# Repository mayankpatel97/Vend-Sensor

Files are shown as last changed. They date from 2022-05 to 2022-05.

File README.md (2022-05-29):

Vend sensor is used to detect an item has vend in Vending Machines. It sense the product and send a signal to 
the main motherboard, indicating item has vend. Responding to this signal motherboard will stop rotating motor

Every vending machine has a rectangular bucket from where user collects the purchased items. This sensor will 
be installed there, so it can detect and count each and every product dropped by machine in to the bucket.

A vend sensor must be sensitive and fast enough to detect even tiny products. 

The product has two pcbs 
1) Transmitter : An array IR LEDs transmitting a 56Khz modulated signal. This pcb is connected with Receiver board through a cable
2) Receiver : This board consist of IR demodulators connected to an STM32F0 microcontroller.

************************** PCB ****************************************
Receiver PCB 




Transmitter PCB 



************************* Software *************************************

As I mentioned above the circuit is built around STM32F0 microcontroller, it uses HAL drivers.
Follow below steps to make the code working 

1) Download the code and open STM32 Cube file and regenerate the code.
2) Once the code has generated, open the project in keil MDK ARM, and build the code.
3) Then upload the code in the microcontroller. 

for further details contact me at 
mayankpatel468@gmail.com 
or send a whatsapp message on 
+918802846486

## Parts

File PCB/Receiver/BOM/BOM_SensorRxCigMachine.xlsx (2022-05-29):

S.No | Designator | Value | Description | QTY
1 | > C1-C8, C19-C24 | 0.1uF | Capacitor_SMD:C_0805_2012Metric_Pad1.15x1.40mm_HandSolder | 14
2 | > C9, C10 | 10uF | Capacitor_SMD:C_0805_2012Metric_Pad1.15x1.40mm_HandSolder | 2
3 | > C16, C27 | 100uF/25V | Capacitor_THT:CP_Radial_D6.3mm_P2.50mm | 2
4 | D1 | M7 | Diode_SMD:D_SMA | 1
5 | D3 | GREEN | LED_SMD:LED_0805_2012Metric_Pad1.15x1.40mm_HandSolder | 1
6 | D4 | YELLOW | LED_SMD:LED_0805_2012Metric_Pad1.15x1.40mm_HandSolder | 1
7 | > H1, H2 | MountingHole | MountingHole:MountingHole_3.2mm_M3_Pad | 2
8 | J1 | Conn_01x03 | Connector_Molex:Molex_KK-254_AE-6410-03A_1x03_P2.54mm_Vertical | 1
9 | J2 | Conn_02x05_Odd_Even | Connector_PinHeader_1.27mm:PinHeader_2x05_P1.27mm_Vertical | 1
10 | J3 | Conn_01x05 | Connector_PinHeader_2.54mm:PinHeader_1x05_P2.54mm_Vertical | 1
11 | Q2 | BC847 | Package_TO_SOT_SMD:SOT-23 | 1
12 | > R3, R9 | 330E | Resistor_SMD:R_0805_2012Metric_Pad1.15x1.40mm_HandSolder | 2
13 | > R5, R7, R11, R12, R15-R18 | 100E | Resistor_SMD:R_0805_2012Metric_Pad1.15x1.40mm_HandSolder | 8
14 | R8 | 1K | Resistor_SMD:R_0805_2012Metric_Pad1.15x1.40mm_HandSolder | 1
15 | R10 | 10K | Resistor_SMD:R_0805_2012Metric_Pad1.15x1.40mm_HandSolder | 1
16 | > U1-U8 | TSSP4056 | Apogee:tssp4056 | 8
17 | U14 | LD1117S33TR_SOT223 | Package_TO_SOT_SMD:SOT-223-3_TabPin2 | 1
18 | U15 | STM32F030C8Tx | Package_QFP:LQFP-48_7x7mm_P0.5mm | 1

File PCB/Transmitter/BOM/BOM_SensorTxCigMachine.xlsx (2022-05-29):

S.No | Designator | Value | Description | QTY
1 | D1-D8 | IR204A | LED_THT:LED_D5.0mm_IRBlack | 8
2 | H1, H2 | MountingHole | MountingHole:MountingHole_3.2mm_M3_Pad | 2
3 | J1 | Conn_02x05_Odd_Even | Connector_PinSocket_1.27mm:PinSocket_2x05_P1.27mm_Vertical | 1
4 | R1 | R_US | LED_SMD:LED_0805_2012Metric_Pad1.15x1.40mm_HandSolder | 1

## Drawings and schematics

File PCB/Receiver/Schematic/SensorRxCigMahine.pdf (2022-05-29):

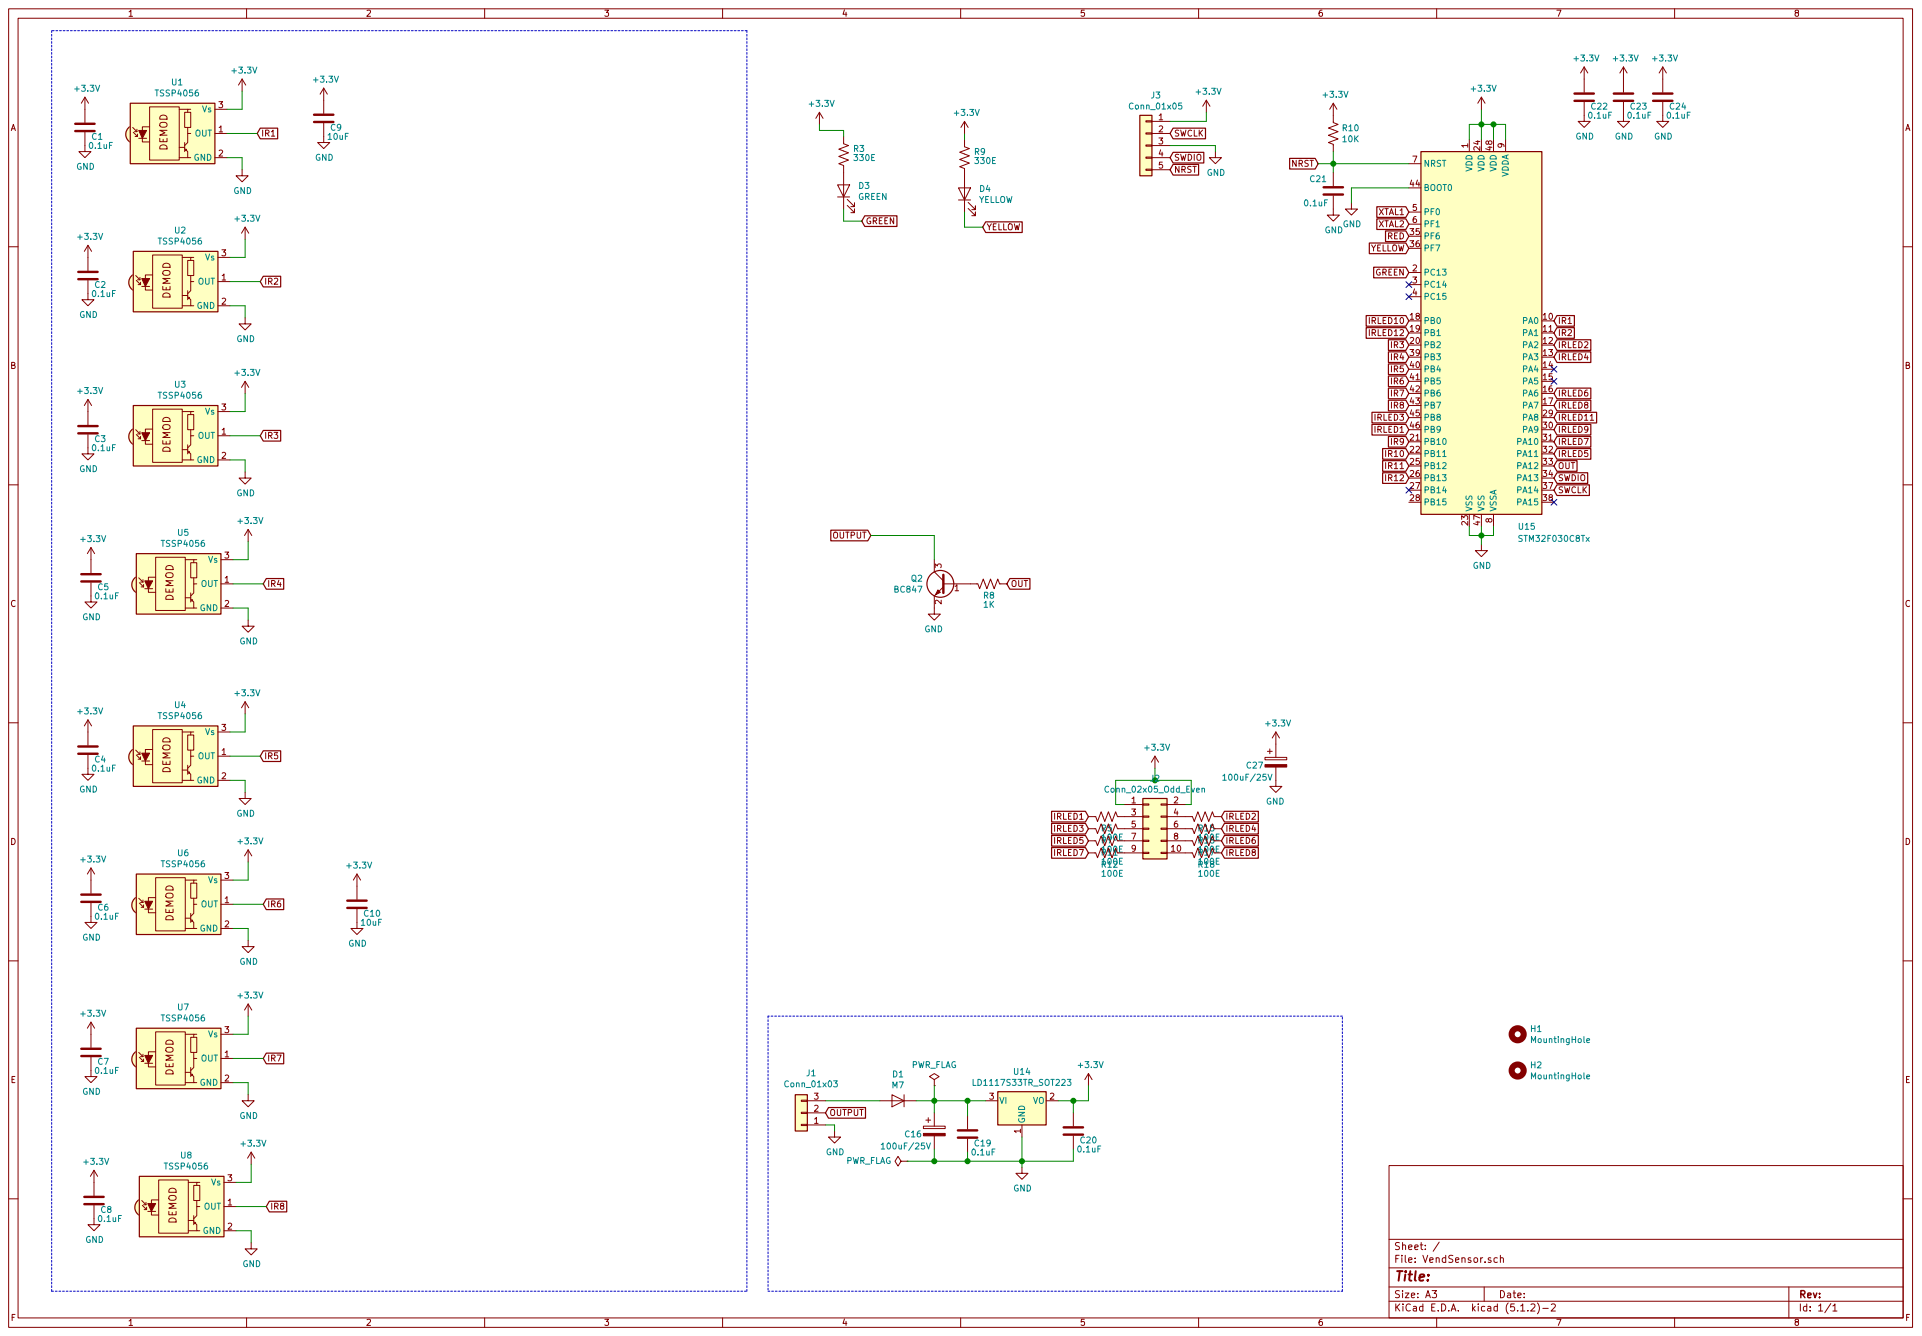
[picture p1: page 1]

PWR_FLAG
Id: 1/1 Title: File: VendSensor.sch Sheet: / D1 M7 C16

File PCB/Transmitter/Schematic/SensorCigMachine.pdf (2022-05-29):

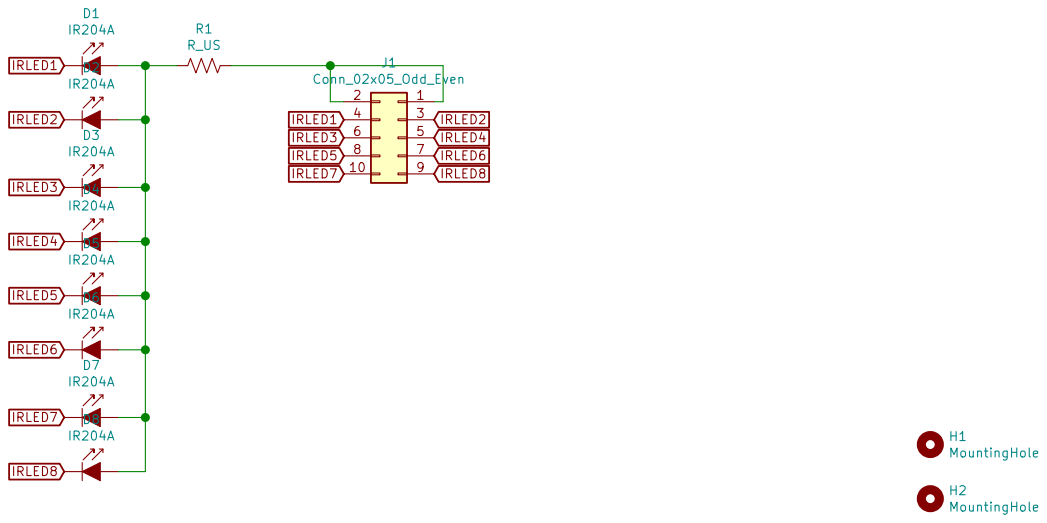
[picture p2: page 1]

Id: 1/1 Title: File: VendSensor.sch Sheet: /

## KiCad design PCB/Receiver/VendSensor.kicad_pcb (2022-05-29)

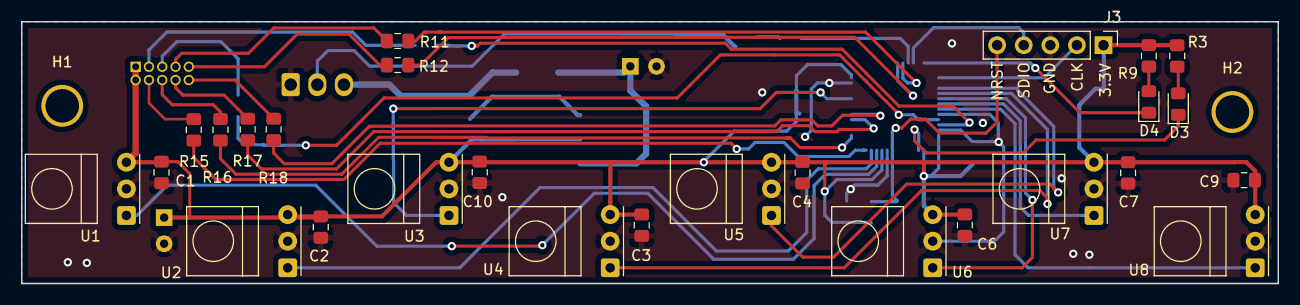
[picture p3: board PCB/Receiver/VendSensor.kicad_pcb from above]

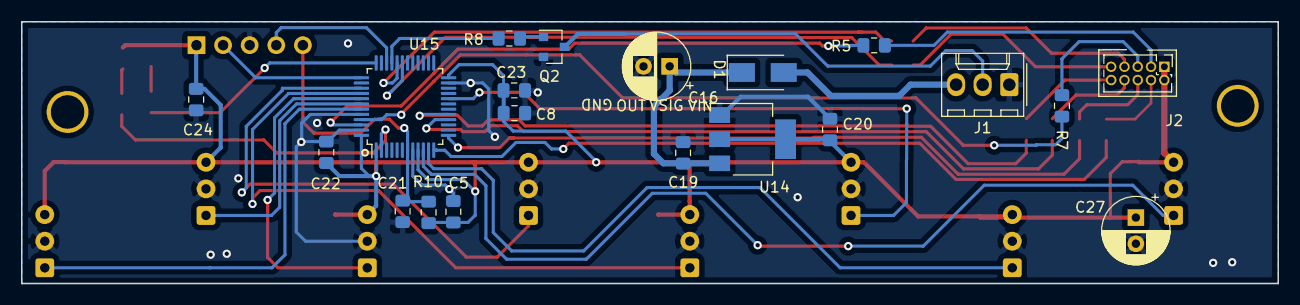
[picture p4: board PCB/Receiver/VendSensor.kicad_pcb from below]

Board: 2 copper layers, 120.0 x 25.0 mm, 49 parts (20 on the bottom side), 38 nets.

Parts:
C1, C2, C3, C4, C5, C6, C7, C8, C19, C20, C21, C22, C23, C24: 0.1uF; C_0805_2012Metric_Pad1.15x1.40mm_HandSolder
C9, C10: 10uF; C_0805_2012Metric_Pad1.15x1.40mm_HandSolder
C16, C27: 100uF/25V; CP_Radial_D6.3mm_P2.50mm
D1: M7; D_SMA
D3: GREEN; LED_0805_2012Metric_Pad1.15x1.40mm_HandSolder
D4: YELLOW; LED_0805_2012Metric_Pad1.15x1.40mm_HandSolder
H1, H2: MountingHole; MountingHole_3.2mm_M3_Pad
J1: Conn_01x03; Molex_KK-254_AE-6410-03A_1x03_P2.54mm_Vertical
J2: Conn_02x05_Odd_Even; PinHeader_2x05_P1.27mm_Vertical
J3: Conn_01x05; PinHeader_1x05_P2.54mm_Vertical
Q2: BC847; SOT-23
R3, R9: 330E; R_0805_2012Metric_Pad1.15x1.40mm_HandSolder
R5, R7, R11, R12, R15, R16, R17, R18: 100E; R_0805_2012Metric_Pad1.15x1.40mm_HandSolder
R8: 1K; R_0805_2012Metric_Pad1.15x1.40mm_HandSolder
R10: 10K; R_0805_2012Metric_Pad1.15x1.40mm_HandSolder
U1, U2, U3, U4, U5, U6, U7, U8: TSSP4056; tssp4056
U14: LD1117S33TR_SOT223; SOT-223-3_TabPin2
U15: STM32F030C8Tx; LQFP-48_7x7mm_P0.5mm

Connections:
+3V3: C1.1, C2.1, C3.1, C4.1, C5.1, C6.1, C7.1, C8.1, C9.1, C10.1, C20.1, C22.1, C23.1, C24.1, C27.1, J2.1, J2.2, J3.1, R3.1, R9.1, R10.1, U1.3, U2.3, U3.3, U4.3, U5.3, U6.3, U7.3, U8.3, U14.2, U15.1, U15.9, U15.24, U15.48
GND: C1.2, C2.2, C3.2, C4.2, C5.2, C6.2, C7.2, C8.2, C9.2, C10.2, C16.2, C19.2, C20.2, C21.2, C22.2, C23.2, C24.2, C27.2, J1.1, J3.3, Q2.2, U1.2, U2.2, U3.2, U4.2, U5.2, U6.2, U7.2, U8.2, U14.1, U15.8, U15.23, U15.44, U15.47
GREEN: D3.1, U15.2
IR1: U1.1, U15.10
IR2: U2.1, U15.11
IR3: U3.1, U15.20
IR4: U5.1, U15.39
IR5: U4.1, U15.40
IR6: U6.1, U15.41
IR7: U7.1, U15.42
IR8: U8.1, U15.43
IRLED1: R5.2, U15.46
IRLED2: R15.1, U15.12
IRLED3: R7.2, U15.45
IRLED4: R16.1, U15.13
IRLED5: R11.2, U15.32
IRLED6: R17.1, U15.16
IRLED7: R12.2, U15.31
IRLED8: R18.1, U15.17
NRST: C21.1, J3.5, R10.2, U15.7
unnamed: C16.1, C19.1, D1.1, U14.3
unnamed: D1.2, J1.3
unnamed: D3.2, R3.2
unnamed: D4.2, R9.2
unnamed: J2.3, R5.1
unnamed: J2.4, R15.2
unnamed: J2.5, R7.1
unnamed: J2.6, R16.2
unnamed: J2.7, R11.1
unnamed: J2.8, R17.2
unnamed: J2.9, R12.1
unnamed: J2.10, R18.2
unnamed: Q2.1, R8.2
OUT: R8.1, U15.33
OUTPUT: J1.2, Q2.3
SWCLK: J3.2, U15.37
SWDIO: J3.4, U15.34
YELLOW: D4.1, U15.36

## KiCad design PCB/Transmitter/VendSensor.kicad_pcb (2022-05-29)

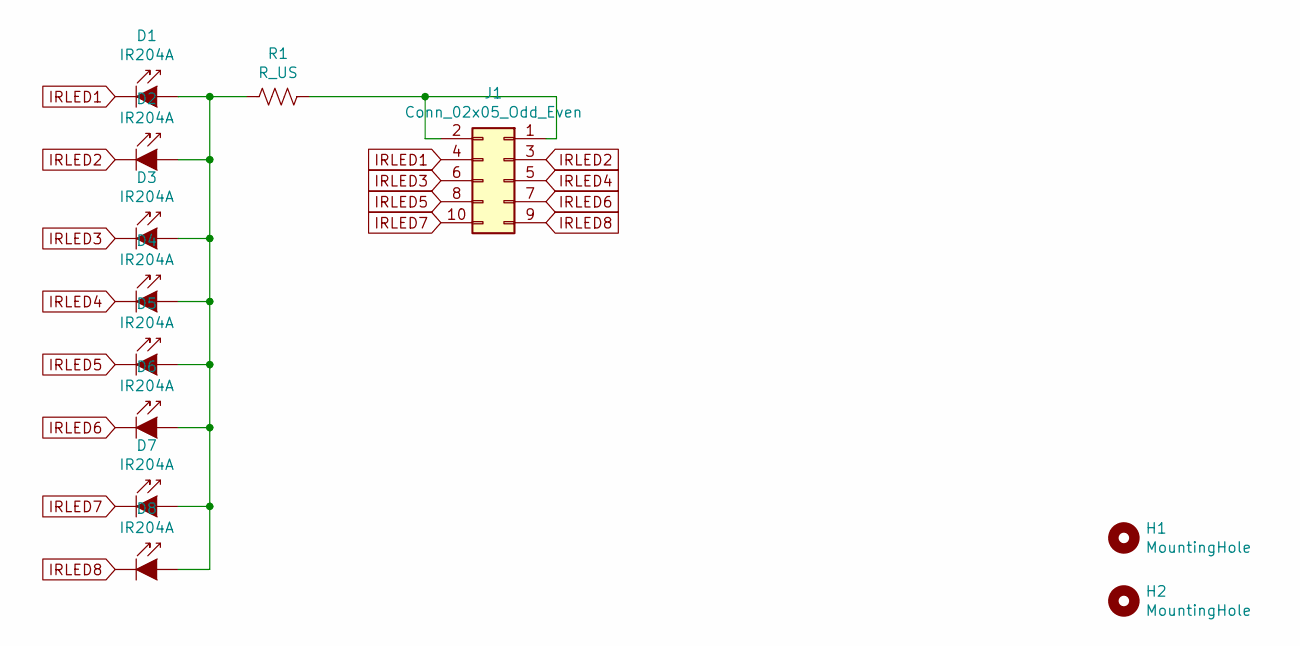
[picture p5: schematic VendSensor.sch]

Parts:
D1, D2, D3, D4, D5, D6, D7, D8: IR204A; LED_D5.0mm_IRBlack
H1, H2: MountingHole; MountingHole_3.2mm_M3_Pad
J1: Conn_02x05_Odd_Even; PinSocket_2x05_P1.27mm_Vertical
R1: R_US; LED_0805_2012Metric_Pad1.15x1.40mm_HandSolder

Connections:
IRLED1: D1.1 (K), J1.4
IRLED2: D2.1 (K), J1.3
IRLED3: D3.1 (K), J1.6
IRLED4: D4.1 (K), J1.5
IRLED5: D5.1 (K), J1.8
IRLED6: D6.1 (K), J1.7
IRLED7: D7.1 (K), J1.10
IRLED8: D8.1 (K), J1.9
unnamed: D1.2 (A), D2.2 (A), D3.2 (A), D4.2 (A), D5.2 (A), D6.2 (A), D7.2 (A), D8.2 (A), R1.2
unnamed: J1.1, J1.2, R1.1

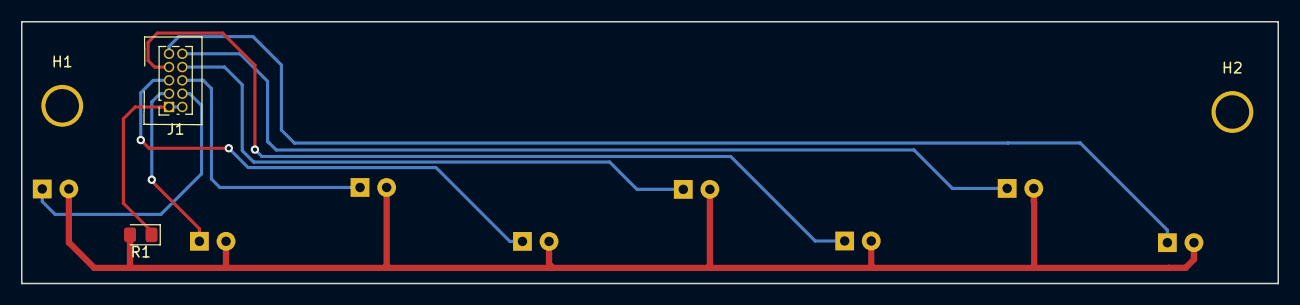
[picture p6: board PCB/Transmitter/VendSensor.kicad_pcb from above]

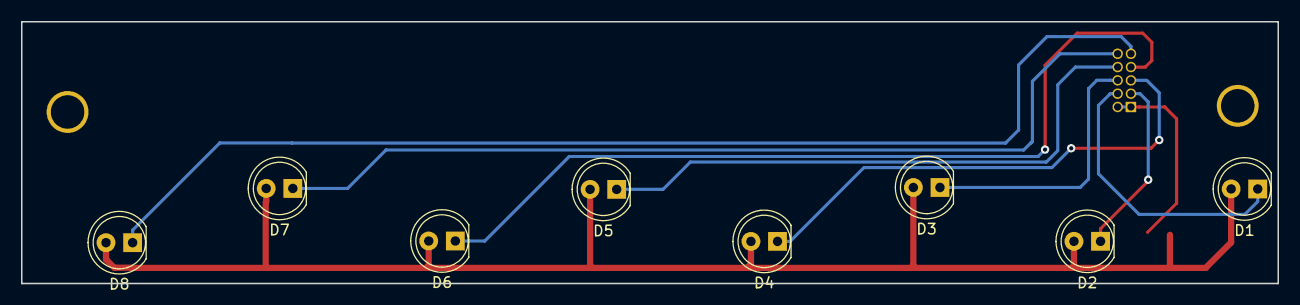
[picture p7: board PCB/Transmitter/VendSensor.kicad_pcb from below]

Board: 2 copper layers, 120.0 x 25.0 mm, 12 parts (8 on the bottom side), 10 nets.

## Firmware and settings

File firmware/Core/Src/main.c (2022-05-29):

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
/* Includes ------------------------------------------------------------------*/
#include "main.h"

TIM_HandleTypeDef htim1;
TIM_HandleTypeDef htim3;
TIM_HandleTypeDef htim6;
TIM_HandleTypeDef htim15;
TIM_HandleTypeDef htim16;
TIM_HandleTypeDef htim17;

void SystemClock_Config(void);
static void MX_GPIO_Init(void);
static void MX_TIM1_Init(void);
static void MX_TIM3_Init(void);
static void MX_TIM15_Init(void);
static void MX_TIM17_Init(void);
static void MX_TIM16_Init(void);
static void MX_TIM6_Init(void);
/* USER CODE BEGIN PFP */
#define TIMER1 1
#define TIMER2 2
#define TIMER3 3

#define CHANNEL1 1
#define CHANNEL2	2
#define CHANNEL3	3
#define CHANNEL4	4

#define PWM_DISABLE_VALUE 0
#define PWM_ENABLE_VALUE 106

#define MIN_VAL 20
#define MAX_VAL 28

#define DEF_LED2_TIMEOUT 25
/* USER CODE END PFP */

/* USER CODE BEGIN 0 */
	#define DEF_BUZZER_ON_TIMEOUT 100
	#define MAX_SENSORS 12
	
	volatile unsigned char Sense,BuzzerOnTimeout;
	
	
unsigned char IRSelect;
unsigned char BlueLedTimeout,Led1Timeout,Led2Timeout,PulseDropCount,PulseDropCount1;
_Bool VendSensed,CheckIR,GreenLedOn;

volatile unsigned int MiniTicks,SmallTicks,SmallTickOver,OneSecOver;
_Bool Ms100_Over;

unsigned int SensorTimeout[MAX_SENSORS],PowerOnTimeout;
unsigned char ChannelSensed[MAX_SENSORS];
volatile unsigned char i,c;
volatile unsigned char MicroSeconds;
volatile unsigned int PulseLength[MAX_SENSORS],TempPulseLength,MinPulseLength,MaxPulseLength;
//void PWM_Config(unsigned char TIMER,unsigned char Channel,unsigned int Value);

void Generate_Burst(unsigned char bTIMER,unsigned char bChannel);
void Generate_Burst2(unsigned char bTIMER,unsigned char bChannel);

void Delay10MicroSeconds(unsigned int uSeconds);

unsigned char SenseThroughMaxMin;
/* USER CODE END 0 */

/**
  * @brief  The application entry point.
  * @retval int
  */
int main(void)
{
  /* MCU Configuration--------------------------------------------------------*/

  /* Reset of all peripherals, Initializes the Flash interface and the Systick. */
  HAL_Init();

  /* Configure the system clock */
  SystemClock_Config();

  /* Initialize all configured peripherals */
  MX_GPIO_Init();
  MX_TIM1_Init();
  MX_TIM3_Init();
  MX_TIM15_Init();
  MX_TIM17_Init();
  MX_TIM16_Init();
  MX_TIM6_Init();
  /* USER CODE BEGIN 2 */
	HAL_Delay(100);
	//HAL_GPIO_WritePin(RED_LED_GPIO_Port,RED_LED_Pin,GPIO_PIN_RESET);
	
	HAL_TIM_Base_Start_IT(&htim6);
	HAL_TIM_Base_Start(&htim3);
	HAL_TIM_Base_Start(&htim1);
	HAL_TIM_Base_Start(&htim17);
	HAL_TIM_Base_Start(&htim15);
	HAL_TIM_Base_Start(&htim16);
	
	HAL_TIM_PWM_Stop(&htim15,TIM_CHANNEL_1);
	HAL_TIM_PWM_Stop(&htim17,TIM_CHANNEL_1);
	HAL_TIM_PWM_Stop(&htim15,TIM_CHANNEL_2);
	HAL_TIM_PWM_Stop(&htim16,TIM_CHANNEL_1);
	HAL_TIM_PWM_Stop(&htim3,TIM_CHANNEL_1);
	HAL_TIM_PWM_Stop(&htim1,TIM_CHANNEL_4);
	HAL_TIM_PWM_Stop(&htim3,TIM_CHANNEL_2);
	HAL_TIM_PWM_Stop(&htim1,TIM_CHANNEL_3);
	HAL_TIM_PWM_Stop(&htim3,TIM_CHANNEL_3);
	HAL_TIM_PWM_Stop(&htim1,TIM_CHANNEL_2);
	HAL_TIM_PWM_Stop(&htim3,TIM_CHANNEL_4);
	HAL_TIM_PWM_Stop(&htim1,TIM_CHANNEL_1);
	
	IRSelect=0;
	PowerOnTimeout = 500;
	MinPulseLength = 0xFFFF;
	MaxPulseLength = 0;
	
  /* USER CODE END 2 */

  /* Infinite loop */
  /* USER CODE BEGIN WHILE */
  while (1)
  {
    /* USER CODE END WHILE */

    /* USER CODE BEGIN 3 */
		
	//	IR_Interrupt=0;
		
		
		switch(IRSelect)
		{
			case 0:

				HAL_TIM_PWM_Start(&htim15,TIM_CHANNEL_1);
			break;
			
			case 1:

				HAL_TIM_PWM_Start(&htim17,TIM_CHANNEL_1);
			break;
			
			case 2:

				HAL_TIM_PWM_Start(&htim15,TIM_CHANNEL_2);
				
			break;
			
			case 3:

				HAL_TIM_PWM_Start(&htim16,TIM_CHANNEL_1);
				
			break;
			
			case 4:

				HAL_TIM_PWM_Start(&htim3,TIM_CHANNEL_1);
				
			break;
			
			case 5:

				HAL_TIM_PWM_Start(&htim1,TIM_CHANNEL_4);
				
			break;
			
			case 6:
				HAL_TIM_PWM_Start(&htim3,TIM_CHANNEL_2);
				
			break;
			
			case 7:

				HAL_TIM_PWM_Start(&htim1,TIM_CHANNEL_3);
				
			break;
			
//			case 8:

//				HAL_TIM_PWM_Start(&htim3,TIM_CHANNEL_3);
//				
//			break;
//			
//			case 9:
//				HAL_TIM_PWM_Start(&htim1,TIM_CHANNEL_2);
//				
//			break;
//			
//			case 10:
//				HAL_TIM_PWM_Start(&htim3,TIM_CHANNEL_4);
//				
//			break;
//						
//			case 11:
//				HAL_TIM_PWM_Start(&htim1,TIM_CHANNEL_1);
//				
//			break;
		}
		
		Delay10MicroSeconds(2);
		//HAL_Delay(2);
		
		switch(IRSelect)
		{
			case 0:

				HAL_TIM_PWM_Stop(&htim15,TIM_CHANNEL_1);
			break;
			
			case 1:

				HAL_TIM_PWM_Stop(&htim17,TIM_CHANNEL_1);
			break;
			
			case 2:

				HAL_TIM_PWM_Stop(&htim15,TIM_CHANNEL_2);
				
			break;
			
			case 3:

				HAL_TIM_PWM_Stop(&htim16,TIM_CHANNEL_1);
				
			break;
			
			case 4:

				HAL_TIM_PWM_Stop(&htim3,TIM_CHANNEL_1);
				
			break;
			
			case 5:

				HAL_TIM_PWM_Stop(&htim1,TIM_CHANNEL_4);
				
			break;
			
			case 6:
				HAL_TIM_PWM_Stop(&htim3,TIM_CHANNEL_2);
				
			break;
			
			case 7:

				HAL_TIM_PWM_Stop(&htim1,TIM_CHANNEL_3);
				
			break;
			
//			case 8:

//				HAL_TIM_PWM_Stop(&htim3,TIM_CHANNEL_3);
//				
//			break;
//			
//			case 9:
//				HAL_TIM_PWM_Stop(&htim1,TIM_CHANNEL_2);
//				
//			break;
//			
//			case 10:
//				HAL_TIM_PWM_Stop(&htim3,TIM_CHANNEL_4);
//				
//			break;
//						
//			case 11:
//				HAL_TIM_PWM_Stop(&htim1,TIM_CHANNEL_1);
//				
//			break;
		}
		
		//Delay10MicroSeconds(12);
		//HAL_Delay(2);
		
		
		IRSelect++;
		if(IRSelect >= MAX_SENSORS)
		{
			IRSelect=0;
		}
		
	
		if(SmallTickOver)
		{
			SmallTickOver=0;
			
			if(Led2Timeout > 0)
			{
				Led2Timeout--;
				if(Led2Timeout == 0)
				{
					//HAL_GPIO_WritePin(RED_LED_GPIO_Port,RED_LED_Pin,GPIO_PIN_SET);
					HAL_GPIO_WritePin(OUT_GPIO_Port,OUT_Pin,GPIO_PIN_RESET);
				}
			}
			
			if(BuzzerOnTimeout > 0)
			{
				BuzzerOnTimeout--;
				if(BuzzerOnTimeout == 0)
				{
					HAL_GPIO_WritePin(GREEN_LED_GPIO_Port,GREEN_LED_Pin,GPIO_PIN_SET);
				}
				
			}
			
			if(PowerOnTimeout>0)
			{
				PowerOnTimeout--;
			}
			else 
			{
				//
				/*
				MinPulseLength = TempPulseLength;
					}
					
					if(TempPulseLength > MaxPulseLength)
					{
						MaxPulseLength 
				*/
				
				if(OneSecOver)
				{
					OneSecOver=0;
					
					if(MinPulseLength < MIN_VAL )
					{
						HAL_GPIO_WritePin(YELLOW_LED_GPIO_Port,YELLOW_LED_Pin,GPIO_PIN_RESET);
						
//						if(SenseThroughMaxMin ==0)
//						{
//							HAL_GPIO_WritePin(OUT_GPIO_Port,OUT_Pin,GPIO_PIN_SET);
//							Led2Timeout=DEF_LED2_TIMEOUT;
//							SenseThroughMaxMin=1;
//						}
					}
					else if(MaxPulseLength > MAX_VAL)
					{
						HAL_GPIO_WritePin(YELLOW_LED_GPIO_Port,YELLOW_LED_Pin,GPIO_PIN_RESET);
//						if(SenseThroughMaxMin ==0)
//						{
//							HAL_GPIO_WritePin(OUT_GPIO_Port,OUT_Pin,GPIO_PIN_SET);
//							Led2Timeout=DEF_LED2_TIMEOUT;
//							SenseThroughMaxMin=1;
//						}
					}
					else 
					{
						HAL_GPIO_WritePin(YELLOW_LED_GPIO_Port,YELLOW_LED_Pin,GPIO_PIN_SET);
						SenseThroughMaxMin=0;
					}
					
					MinPulseLength = 0xFFFF;
					MaxPulseLength = 0;
				}
				
			}
		}
		
		
  }
  /* USER CODE END 3 */
}

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
/* USER CODE BEGIN 4 */

void ActChannelInterrupt(unsigned char channelNum)
{
	if( (SensorTimeout[channelNum] > MAX_VAL) || (SensorTimeout[channelNum] < MIN_VAL) )
	{
		//HAL_GPIO_WritePin(RED_LED_GPIO_Port,RED_LED_Pin,GPIO_PIN_RESET);
		HAL_GPIO_WritePin(OUT_GPIO_Port,OUT_Pin,GPIO_PIN_SET);
		Led2Timeout=DEF_LED2_TIMEOUT;
		
		Sense=1;
	}
	TempPulseLength = PulseLength[channelNum];
	PulseLength[channelNum] = SensorTimeout[channelNum];
	SensorTimeout[channelNum]=0;
}


void HAL_GPIO_EXTI_Callback(uint16_t GPIO_Pin)
{
	Sense=0;
	// IR_Interrupt
	if(GPIO_Pin == GPIO_PIN_0)
	{
		ActChannelInterrupt(0);
	}
	
	else if(GPIO_Pin == GPIO_PIN_1)
	{
		ActChannelInterrupt(1);
	}
	
	else if(GPIO_Pin == GPIO_PIN_2)
	{
		ActChannelInterrupt(2);
	}
	
	else if(GPIO_Pin == GPIO_PIN_3)
	{
		ActChannelInterrupt(3);
	}
	
	else if(GPIO_Pin == GPIO_PIN_4)
	{
		ActChannelInterrupt(4);
	}
	
	else if(GPIO_Pin == GPIO_PIN_5)
	{
		ActChannelInterrupt(5);
	}
	
	else if(GPIO_Pin == GPIO_PIN_6)
	{
		ActChannelInterrupt(6);
	}
	
	else if(GPIO_Pin == GPIO_PIN_7)
	{	
		ActChannelInterrupt(7);
	}
	
//	if(GPIO_Pin == GPIO_PIN_10)
//	{
//		ActChannelInterrupt(8);
//	}
//	
//	if(GPIO_Pin == GPIO_PIN_11)
//	{
//		ActChannelInterrupt(9);
//	}
//	else if(GPIO_Pin == GPIO_PIN_12)
//	{
//		ActChannelInterrupt(10);
//	}
//	else if(GPIO_Pin == GPIO_PIN_13)
//	{
//		ActChannelInterrupt(11);
//	}
//	
	
	if(Sense)
	{

		HAL_GPIO_WritePin(GREEN_LED_GPIO_Port,GREEN_LED_Pin,GPIO_PIN_RESET);
		BuzzerOnTimeout = DEF_BUZZER_ON_TIMEOUT;
		

		
	}
	
	if(PowerOnTimeout == 0)
	{
		if(TempPulseLength < MinPulseLength)
		{
			MinPulseLength = TempPulseLength;
		}
		
		if(TempPulseLength > MaxPulseLength)
		{
			MaxPulseLength = TempPulseLength;
		}
	}
	
}


void HAL_TIM_PeriodElapsedCallback(TIM_HandleTypeDef *htim)
{
	if(htim == &htim6)
	{
		// 10uS interrupt
		MiniTicks++;
		if(MicroSeconds > 0)
			MicroSeconds--;

		for(i=0;i<MAX_SENSORS;i++)
		{
			if(SensorTimeout[i] < 0xFFFF)
			{
				SensorTimeout[i]++;
			}
		}
		
		if(MiniTicks >= 20)
		{
			MiniTicks=0; // 1Ms Over
			SmallTicks++;
			
			SmallTickOver=1;
			
			if( (SmallTicks % 100) == 0)
			{
				Ms100_Over=1;
			}
			
			
			if(SmallTicks >= 1000)
			{
				SmallTicks=0;
				OneSecOver=1;
				//HAL_GPIO_TogglePin(YELLOW_LED_GPIO_Port,YELLOW_LED_Pin);
			}
		}
	}
}

void Delay10MicroSeconds(unsigned int uSeconds)
{
	MicroSeconds=uSeconds;
	while(MicroSeconds > 0);
}

/* USER CODE END 4 */
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


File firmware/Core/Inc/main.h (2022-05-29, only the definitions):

#define GREEN_LED_Pin GPIO_PIN_13
#define GREEN_LED_GPIO_Port GPIOC
#define OUT_Pin GPIO_PIN_12
#define OUT_GPIO_Port GPIOA
#define RED_LED_Pin GPIO_PIN_6
#define RED_LED_GPIO_Port GPIOF
#define YELLOW_LED_Pin GPIO_PIN_7
#define YELLOW_LED_GPIO_Port GPIOF

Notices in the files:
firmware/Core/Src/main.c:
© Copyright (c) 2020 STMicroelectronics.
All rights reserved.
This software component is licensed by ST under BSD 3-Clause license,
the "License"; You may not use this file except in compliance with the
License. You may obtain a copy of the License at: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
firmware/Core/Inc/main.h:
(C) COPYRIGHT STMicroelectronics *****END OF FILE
